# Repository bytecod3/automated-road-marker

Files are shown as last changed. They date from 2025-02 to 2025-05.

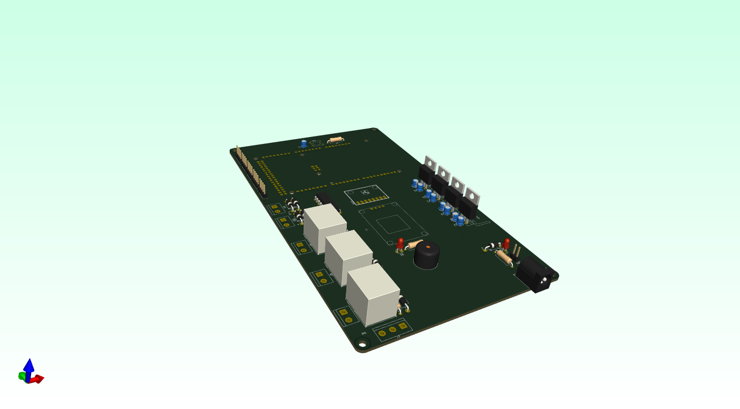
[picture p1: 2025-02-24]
hardware-design/pcb-images/side-view.png

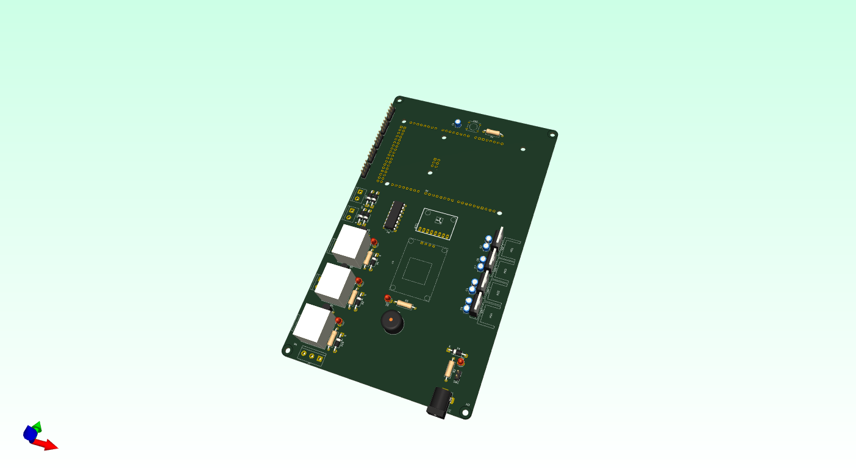
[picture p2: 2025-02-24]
hardware-design/pcb-images/v1-orthogonal.png

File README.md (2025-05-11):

# automated-road-marker
Automated road marker project

## Battery sizing and component voltages 
| Component | Voltage rating (V) | Current rating
| --- | --- | --- |
| Arduino MEGA 2560  | 7-12 | -
| TT 130 accelerator/decelerator motor  | 3-6 | 170mA(at 4.5V)
| HC-SR04 ultrasonic sensor | 5 | 4mA
|  12V Solenoid valve G1/2 DN15 BSPP Pressure Type | 12 | 416mA
| 12V DC 385 high temperature water pump | 12 | 400mA |
| YF-S401 Water Flow Sensor | 5 | 15 mA (at 5V)

Recomended Battery = 12V >2000mAh

## firmware dependencies
The following libraries need to installed in Arduino 
1. LiquidCrystal I2C library by Frank de Brabander
2. I2Cdev

## Following a straight line 
The robot follows a heading that is referenced to where it starts. To do this, 
1. place the robot on the surface you want to paint
2. press the reset button WHILE THE ROBOT IS STATIONARY! There should be no movements or shaking. 
3. The robot should follow a straight heading.
4. To stop the robot, press the ON/OFF button, or disconenct the battery 

5. If using LCD, the screen should show the flow rate.

## Paint system 
The paint sequence is as follows:
1. Once the robot is turned on, it paints at intervals of 5 seconds( this can be changed in the 
code. See code!). This paint sequence produces a dotted line 
2. Pump 1, pump 2 and solenoid are turned on at the same time.
3. Flow rate is measured and displayed. 
4. Process repeats.
5. You can increase the length of the dotted line by increasing the paint interval. (Again, see code 
comments for this)

## ultrasonic designations 

US1 -> Front ultrasonic
US2 -> Right ultrasonic
US3 -> Left ultrasonic
US4 -> Resorvoir level ultrasonic

### Ultrasonic Conclusion
Ultrasonic avidance is not necesssary in the real-world. Why are you painting a road with obstacles??

## Flow meter interrupt pin change
The schematic show flow meter signal connected to pin 10. From tests, pin 10 cannot support
interrupts. Please use pin 2 for the flow meter signal.( See code on flow meter Pin -> in defines. h. If you wish 
to change the pin to pin number 3).

Only pin 2 and 3 can be used for the flow meter.

# LCD library installation
If you cannot find the Arduino-LiquidCrystal-I2C on Arduino Library manager, copy the Arduino-LiquidCrystal-I2C folder into your Arduino installation folder.
You should be able to compile the code with no errors.

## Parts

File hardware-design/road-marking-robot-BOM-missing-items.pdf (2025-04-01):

### road-marking-robot-BOM

# | Value | Reference | Qty | DNP | SHOP

1 | Arduino_Mega2560_R3_Shield | A1 | 1
2 | MPU6050 | ACC1 | 1
3 | Buzzer | BZ1 | 1
4 | 10uf Capcaitor | C1,C2,C3,C4,C5,C6,C7,C8 | 8
5 | 100nF | C9 | 1
6 | 1N4001 | D1,D3,D4,D6,D7,D8,D9,D10 | 8
7 | 3mm Green LED | D2,D5 | 2
8 | 3mm Red LED | D11,D12,D13 | 3
9 | Heat sink | HS1,HS2,HS3,HS4 | 4 | https://www.pixelelectric.com/more-categories/other-accessories/fans-heater-coolers/heat-sink-black-anodized-to-220/
10 | DC Barrel Jack THT PCB mount | J1 | 1 | https://www.pixelelectric.com/more-categories/electronic-components/led-plugs-connectors/plugs-connectors/dc-power-jack-2-1mm-barrel-type-pcb-mount/
11 | u-sonic-1 | J2 | 1
12 | u-sonic-2 | J3 | 1
13 | u-sonic-3 | J4 | 3 | https://bluepacknova.com/product/ultrasonic-sensor/
16 | 3PIN Terminal block | J7 | 2 | https://www.pixelelectric.com/electronic-components/led-plugs-connectors/plugs-connectors/kf301-3p-5-08mm-3-pin-connector-terminal/
17 | 2PIN terminal block | J8,J11,J13 | 3
18 | 2 pin Terminal block | J9 | 3 | https://www.pixelelectric.com/more-categories/electronic-components/led-plugs-connectors/plugs-connectors/kf301-2pin-straight-pin-pcb-screw-block/
20 | SugarCube relay | K1,K2,K3 | 1 | https://bluepacknova.com/product/5v-relay-1-channel/
21 | ROBOT_WHEEL | M2 | 1 | DNP
22 | BC547 transistor | Q2,Q3,Q4 | 5 | https://store.nerokas.co.ke/SKU-845?search=bc547&description=true
23 | 500R resistor | R1,R2,R3,R5,R6 | 5
24 | 10K resistor | R4 | 1
26 | push button pin | SW2 | 1
27 | LM7909_TO220 | U1 | 1 | https://www.pixelelectric.com/more-categories/electronic-components/passive-components/transistor-mosfet/l7809cv-high-power-voltage-regulator/
28 | LM7812_TO220 | U2 | 1 | https://www.pixelelectric.com/more-categories/electronic-components/passive-components/transistor-mosfet/l7912cv-high-power-voltage-regulator/
29 | LM7805_TO220 | U3 | 1 | https://www.pixelelectric.com/more-categories/electronic-components/passive-components/transistor-mosfet/l7905cv-high-power-voltage-regulator/
30 | LM7806_TO220 | U4 | 1 | https://www.pixelelectric.com/more-categories/electronic-components/passive-components/transistor-mosfet/l7806cv-high-power-voltage-regulator/
31 | NE06M GPS Module | U5 | 1 | https://bluepacknova.com/product/gy-neo-6m-gps-active-ceramic-antenna-module/
32 | L293D Motor driver chip | U6 | 1
33 | Heat shrink tubing 5mm | | 3 meters
34 | M3 philips screws | 8 | Source locally
35 | 1cm standoffs | 8 | Source locally
36 | PCB Copper clads single side 20x15 cm | 2
37 | Hydrogen peroxide | 2 cans
38 | Dilute HCL | 1 liter
39 | Male header pins single row 2.54mm pitch | 8 strips
40 | 20AWG copper wire | 4 meters
41 | Soldering wire | 5 meters
42 | Soldering flux | 1 bottle
43 | Female header pins single row 2.54mm pitch | 4 strips | https://bluepacknova.com/product/female-header-pin-2-0-mm/

BOM-revised-missing-items-18.03.25

### Page 1

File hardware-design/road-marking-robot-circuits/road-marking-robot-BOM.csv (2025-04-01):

# | Value | Reference | Qty | DNP
1 | Arduino_Mega2560_R3_Shield | A1 | 1
2 | MU6060 | ACC1 | 1
3 | Buzzer | BZ1 | 1
4 | 10uf Capcaitor | C1,C2,C3,C4,C5,C6,C7,C8 | 8
5 | 100nF | C9 | 1
6 | 1N4001 | D1,D3,D4,D6,D7,D8,D9,D10 | 8
7 | 3mm Green LED | D2,D5 | 2
8 | 3mm Red LED | D11,D12,D13 | 3
9 | Heat sink | HS1,HS2,HS3,HS4 | 4
10 | DC Barrel Jack THT | J1 | 1
11 | u-sonic-1 | J2 | 1
12 | u-sonic-2 | J3 | 1
13 | u-sonic-3 | J4 | 1
14 | u-sonic-4 | J5 | 1
15 | u-sonic-5 | J6 | 1
16 | 3PIN Terminal block | J7 | 1
17 | 2PIN terminal block | J8,J11,J13 | 3
18 | 2 pin Terminal block | J9 | 1
19 | 2 PIN terminal Block | J10 | 1
20 | SugarCube relay | K1,K2,K3 | 3
21 | ROBOT_WHEEL | M2 | 1 | DNP
22 | BC547 transistor | Q2,Q3,Q4 | 3
23 | 500R resistor | R1,R2,R3,R5,R6 | 5
24 | 10K resistor | R4 | 1
25 | 2pin terminal block | SW1 | 1
26 | push button pin | SW2 | 1
27 | LM7909_TO220 | U1 | 1
28 | LM7812_TO220 | U2 | 1
29 | LM7805_TO220 | U3 | 1
30 | LM7806_TO220 | U4 | 1
31 | NE06M GPS Module | U5 | 1
32 | L293D Motor driver chip | U6 | 1

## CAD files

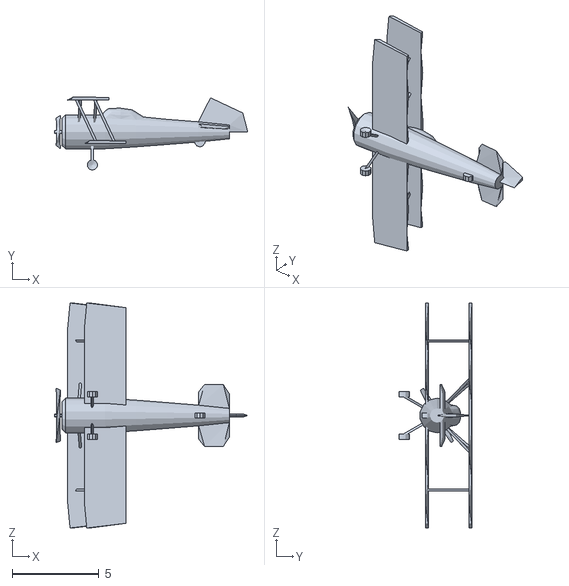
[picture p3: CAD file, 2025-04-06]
firmware/i2cdevlib-master/Arduino/MPU6050/examples/MPU6050_DMP6_using_DMP_V6.12/MPUplane/data/biplane.obj
11.2 x 4.23 x 13.0

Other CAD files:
firmware/i2cdevlib-master/PIC18/MPU6050/Examples/MPU6050_raw.X/l.obj

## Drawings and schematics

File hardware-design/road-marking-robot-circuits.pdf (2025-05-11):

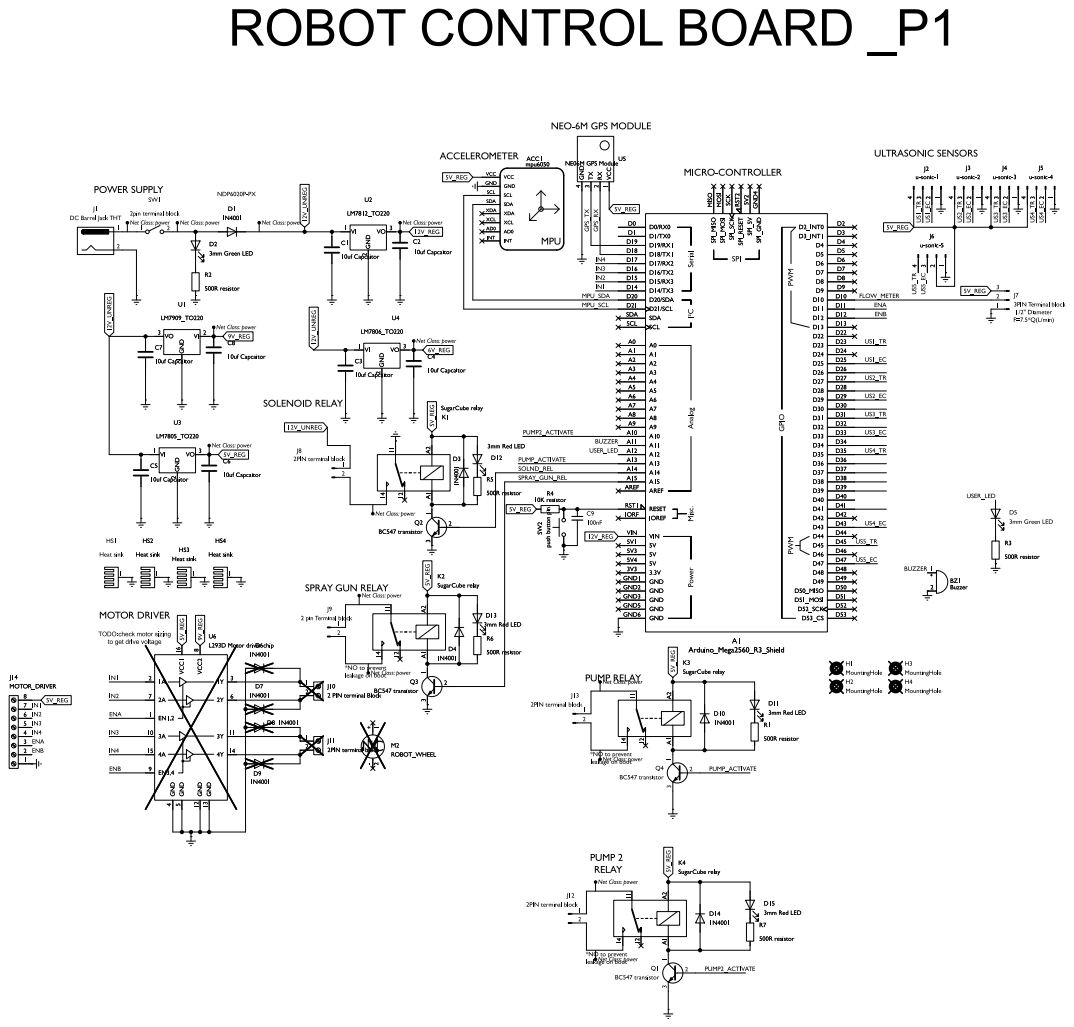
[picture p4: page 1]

leakageon boot ROBOT CONTROL BOARD _P1

leakageon boot SPRAYGUN RELAY

TODO:check motor sizing
to get drive voltage

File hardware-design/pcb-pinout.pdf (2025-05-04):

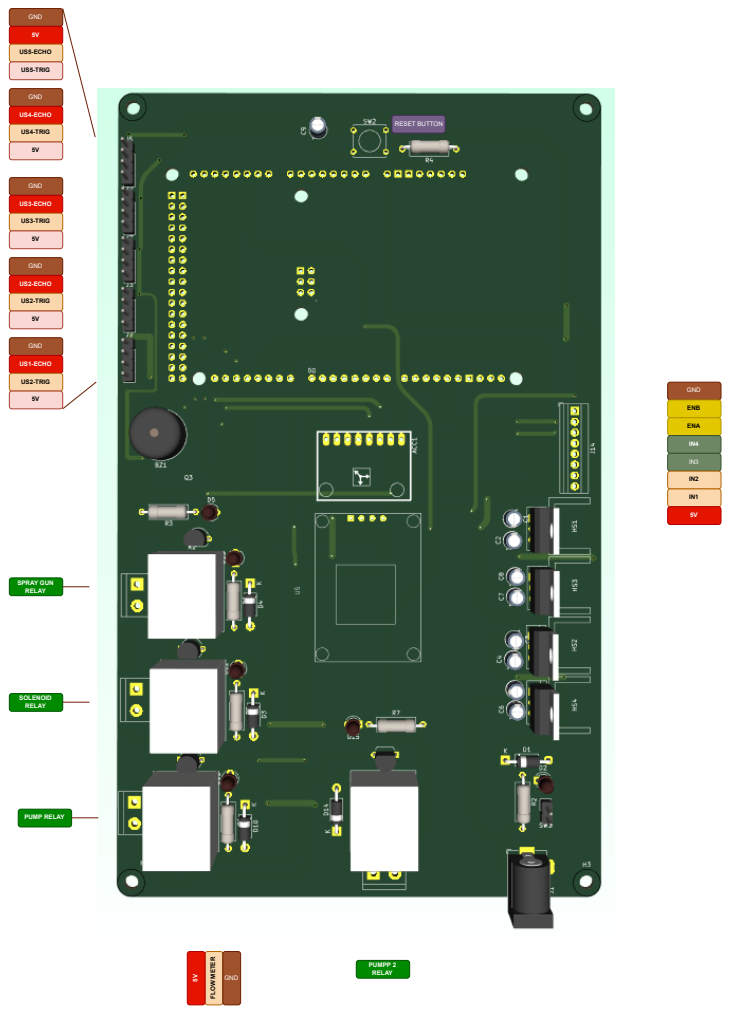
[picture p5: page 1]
GND; US5-ECHO; US5-TRIG; US4-ECHO; US4-TRIG; US3-ECHO; US3-TRIG; US2-ECHO; US2-TRIG; US1-ECHO; SPRAY GUN RELAY; PUMP RELAY; SOLENOID RELAY; PUMPP 2 RELAY; ENB; ENA; RESET BUTTON; FLOW METER

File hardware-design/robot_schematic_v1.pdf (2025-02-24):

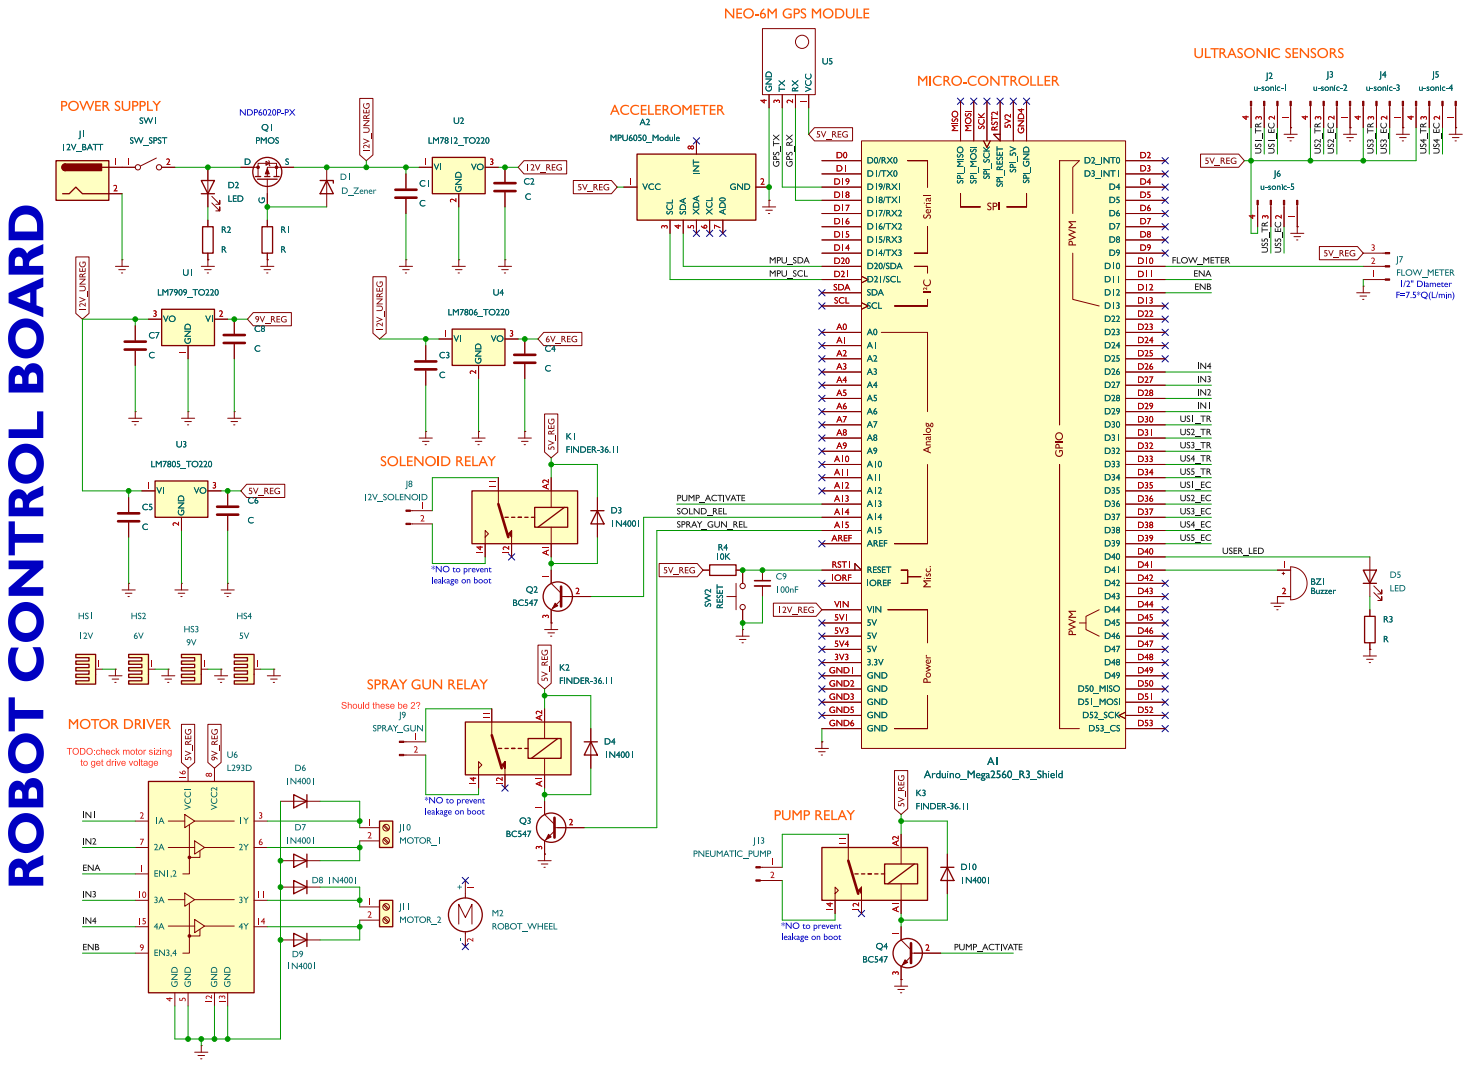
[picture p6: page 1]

Should these be 2? ROBOT CONTROL BOARD

leakageon boot TODO:check motor sizing
to get drive voltage

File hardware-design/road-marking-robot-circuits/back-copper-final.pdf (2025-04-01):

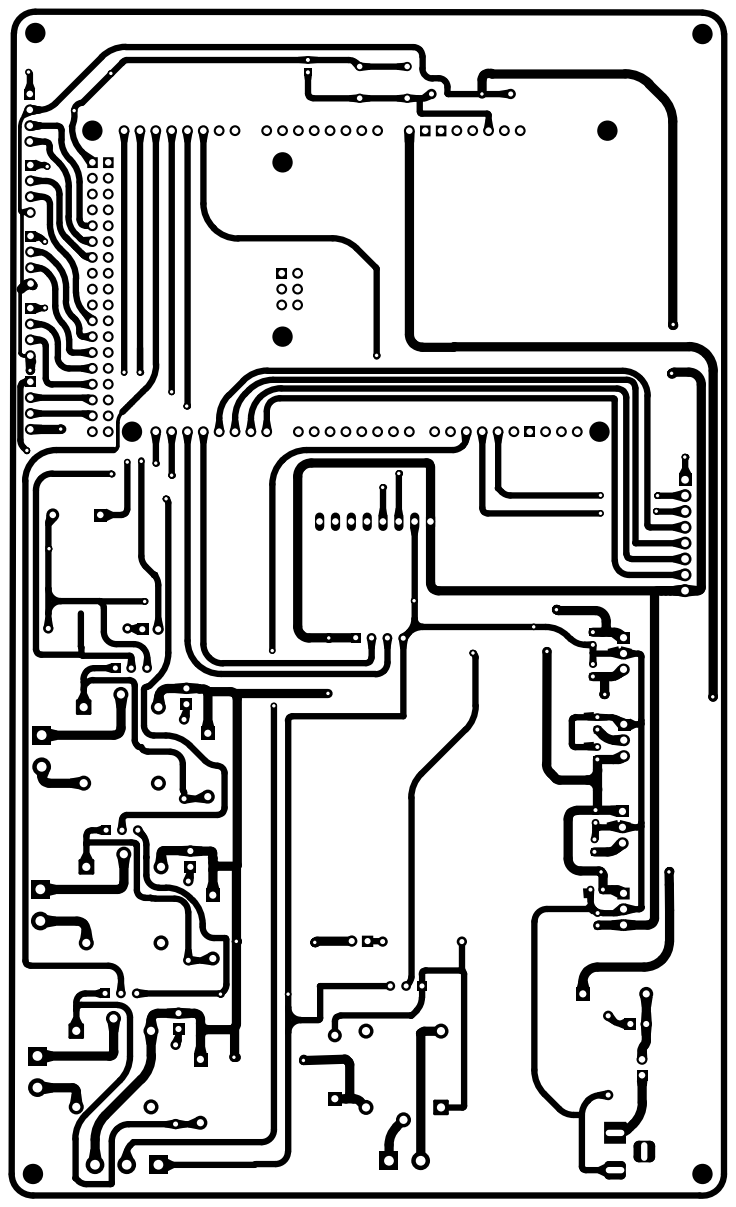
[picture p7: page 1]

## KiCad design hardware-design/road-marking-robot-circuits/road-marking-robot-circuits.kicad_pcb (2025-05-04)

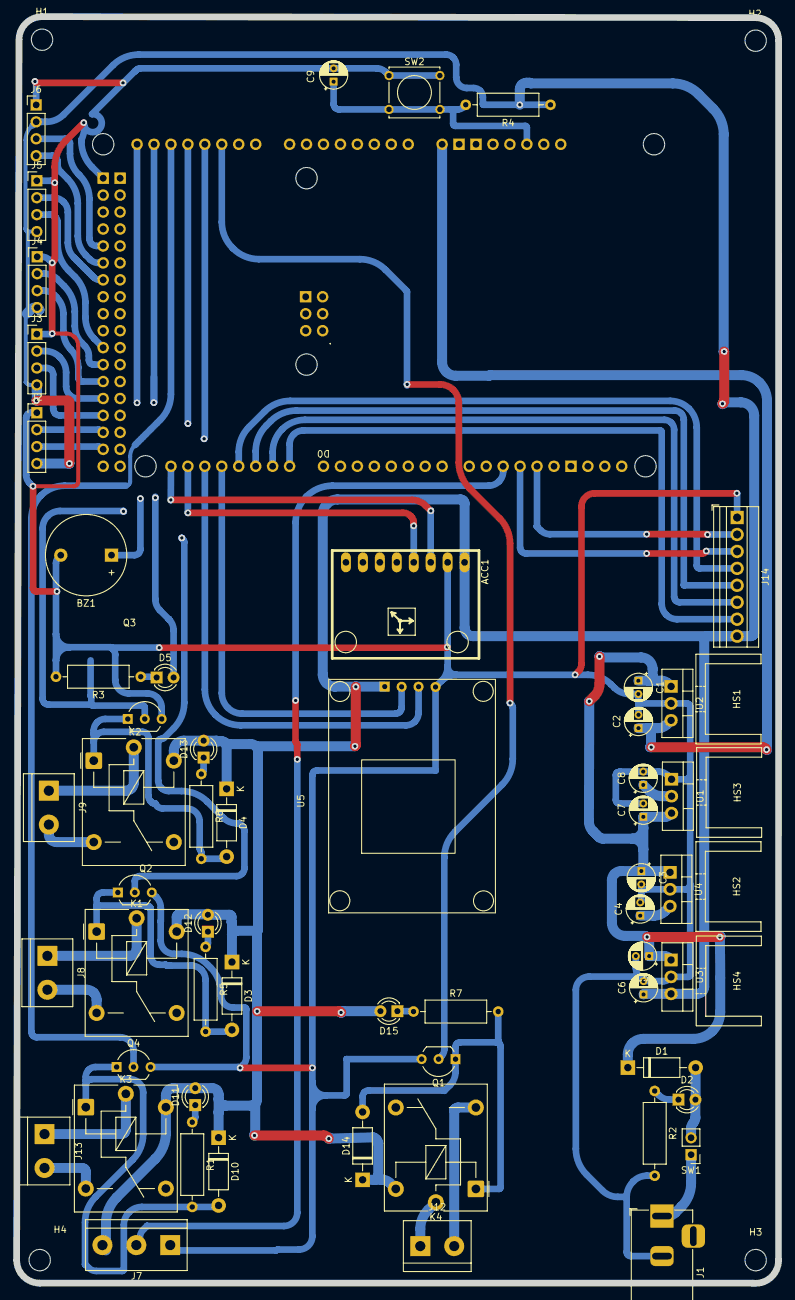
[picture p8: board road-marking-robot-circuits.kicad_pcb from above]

Board: 2 copper layers, 114.2 x 189.8 mm, 65 parts (0 on the bottom side), 53 nets.

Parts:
A1: Arduino_Mega2560_R3_Shield
ACC1: mpu6050; GY-521
BZ1: Buzzer; Buzzer_12x9.5RM7.6
C1, C2, C3, C4, C5, C6, C7, C8: 10uf Capcaitor; CP_Radial_D4.0mm_P2.00mm
C9: 100nF; CP_Radial_D4.0mm_P2.00mm
D1, D3, D4, D10, D14: 1N4001; D_DO-41_SOD81_P10.16mm_Horizontal
D2, D5: 3mm Green LED; LED_D3.0mm
D11, D12, D13, D15: 3mm Red LED; LED_D3.0mm
H1, H2, H3, H4: MountingHole; MountingHole_3.2mm_M3
HS1, HS2, HS3, HS4: Heat sink; Heatsink_Stonecold_HS-S02_13.21x9.53mm
J1: DC Barrel Jack THT; BarrelJack_Horizontal
J2: u-sonic-1; PinHeader_1x04_P2.54mm_Vertical
J3: u-sonic-2; PinHeader_1x04_P2.54mm_Vertical
J4: u-sonic-3; PinHeader_1x04_P2.54mm_Vertical
J5: u-sonic-4; PinHeader_1x04_P2.54mm_Vertical
J6: u-sonic-5; PinHeader_1x04_P2.54mm_Vertical
J7: 3PIN Terminal block; TerminalBlock_bornier-3_P5.08mm
J8, J12, J13: 2PIN terminal block; TerminalBlock_bornier-2_P5.08mm
J9: 2 pin Terminal block; TerminalBlock_bornier-2_P5.08mm
J14: MOTOR_DRIVER; TerminalBlock_Xinya_XY308-2.54-8P_1x08_P2.54mm_Horizontal
K1, K2, K3, K4: SugarCube relay; Relay_SPDT_Finder_36.11
Q1, Q2, Q3, Q4: BC547 transistor; TO-92_Inline_Wide
R1, R2, R3, R5, R6, R7: 500R resistor; R_Axial_DIN0309_L9.0mm_D3.2mm_P12.70mm_Horizontal
R4: 10K resistor; R_Axial_DIN0309_L9.0mm_D3.2mm_P12.70mm_Horizontal
SW1: 2pin terminal block; PinHeader_1x02_P2.54mm_Vertical
SW2: push button pin; SW_Tactile_Straight_KSA0Axx1LFTR
U1: LM7909_TO220; TO-220-3_Vertical
U2: LM7812_TO220; TO-220-3_Vertical
U3: LM7805_TO220; TO-220-3_Vertical
U4: LM7806_TO220; TO-220-3_Vertical
U5: NE06M GPS Module; NEO-6M-GPS-MODULE

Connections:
5V_REG: ACC1.VCC, C6.1, D3.1 (K), D4.1 (K), D10.1 (K), D11.2 (A), D12.2 (A), D13.2 (A), D14.1 (K), D15.2 (A), J2.4, J3.4, J4.4, J5.4, J6.2, J7.3, J14.8, K1.A2, K2.A2, K3.A2, K4.A2, R4.1, U3.3 (VO), U5.1 (VCC)
6V_REG: C4.1, U4.3 (VO)
9V_REG: C8.1, U1.2 (VI)
12V_REG: A1.VIN, C2.1, U2.3 (VO)
12V_UNREG: C1.1, C3.1, C5.1, C7.1, D1.1 (K), J8.1, U1.3 (VO), U2.1 (VI), U3.1 (VI), U4.1 (VI)
/BUZZER: A1.A11, BZ1.1 (+)
/ENA: A1.D11, J14.3
/ENB: A1.D12, J14.2
/FLOW_METER: A1.D10, J7.2
/GPS_RX: A1.D18 (D18/TX1), U5.2 (RX)
/GPS_TX: A1.D19 (D19/RX1), U5.3 (TX)
/IN1: A1.D14 (D14/TX3), J14.7
/IN2: A1.D15 (D15/RX3), J14.6
/IN3: A1.D16 (D16/TX2), J14.5
/IN4: A1.D17 (D17/RX2), J14.4
/MPU_SCL: A1.D21 (D21/SCL), ACC1.SCL
/MPU_SDA: A1.D20 (D20/SDA), ACC1.SDA
/PUMP2_ACTIVATE: A1.A10, Q1.2 (B)
/PUMP_ACTIVATE: A1.A13, Q4.2 (B)
/SOLND_REL: A1.A14, Q2.2 (B)
/SPRAY_GUN_REL: A1.A15, Q3.2 (B)
/US1_EC: A1.D25, J2.2
/US1_TR: A1.D23, J2.3
/US2_EC: A1.D29, J3.2
/US2_TR: A1.D27, J3.3
/US3_EC: A1.D33, J4.2
/US3_TR: A1.D31, J4.3
/US4_EC: A1.D43, J5.2
/US4_TR: A1.D35, J5.3
/US5_EC: A1.D47, J6.3
/US5_TR: A1.D45, J6.4
/USER_LED: A1.A12, D5.2 (A)
Earth: A1.GND6 (GND), ACC1.GND, BZ1.2 (-), C1.2, C2.2, C3.2, C4.2, C5.2, C6.2, C7.2, C8.2, C9.2, J1.2, J2.1, J3.1, J4.1, J5.1, J6.1, J7.1, J14.1, K1.11, Q1.3 (E), Q2.3 (E), Q3.3 (E), Q4.3 (E), R2.2, R3.2, SW2.1, U1.1 (GND), U2.2 (GND), U3.2 (GND), U4.2 (GND), U5.4 (GND)
unnamed: A1.RST1 (RESET), C9.1, R4.2, SW2.2
unnamed: D1.2 (A), D2.2 (A), SW1.2 (B)
unnamed: D2.1 (K), R2.1
unnamed: D3.2 (A), K1.A1, Q2.1 (C), R5.2
unnamed: D4.2 (A), K2.A1, Q3.1 (C), R6.2
unnamed: D5.1 (K), R3.1
unnamed: D10.2 (A), K3.A1, Q4.1 (C), R1.2
unnamed: D11.1 (K), R1.1
unnamed: D12.1 (K), R5.1
unnamed: D13.1 (K), R6.1
unnamed: D14.2 (A), K4.A1, Q1.1 (C), R7.2
unnamed: D15.1 (K), R7.1
unnamed: J8.2, K1.14
unnamed: J9.1, K2.11
unnamed: J9.2, K2.14
unnamed: J12.1, K4.11
unnamed: J12.2, K4.14
unnamed: J13.1, K3.11
unnamed: J13.2, K3.14
unnamed: J1.1, SW1.1 (A)

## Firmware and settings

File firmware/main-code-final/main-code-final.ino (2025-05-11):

#include "defines.h"
#include <Wire.h>
#include "I2Cdev.h"

#define USE_LCD 1 // if you are using an LCD, set this line to 1, otherwise set to 0

#if USE_LCD
  #include <LiquidCrystal_I2C.h>
  LiquidCrystal_I2C lcd(0x27, 16, 2);
#endif

#define MOTOR_ENABLE 1 // must be set to 1 for the motors to run
#define MPU_ENABLE 1  // must be set to 1 for the MPU to be read


unsigned long paint_interval = 5000; // change this interval to change the length of the line painted
unsigned long previous_paint_time = 0;
unsigned long current_paint_time = 0;

// this is the variable used to turn on and off the psint system -> pump1, pump2 and solenoid
// the activation of the paint system must be non-blocking 
// so that the robot stays in motion whie painting
uint8_t paint_system_state = 0; 

/**
 * 
 * states 
 IDLE - on but not painting, buzz twice,blink at 1 second
 PAINTING - actively checking straight line and running paint system, blink at 200ms
 length between IDLE and START_PAINT ~10 seconds 
 measure distance painted?
 * FLOW
 * wait for 10 seconds after setup 
 * Read the IMU 
 * Activate the paint system while checking the straightness of the line 
 * Apply PID to motor while painting 
 * 
 * For demo: paint for 30 seconds then stop 
 * deactivate paint system 
 * state == DONE_PAINTING
 * buzz 3 times at 400ms
 * blink at 1Hz
 */

 
/**
 * Sensor read functions 
 */
void read_gps_cordinates();
void get_flow_rate();

/**
 * Paint system Relay control functions 
 */
void activate_solenoid_relay(uint8_t state);
void activate_pump_one_relay(uint8_t state);
void activate_pump_two_relay(uint8_t state);
void deactivate_solenoid_relay(uint8_t state);
void deactivate_pump_one_relay(uint8_t state);
void deactivate_pump_two_relay(uint8_t state);

void initialize_hardware_pins();
void blink_non_blocking(uint16_t);
void buzz_non_blocking(uint16_t);
void onboard_blink_non_blocking();

/**
 * set pinmodes
 */
void initialize_hardware_pins() {
  pinMode(PUMP_ONE_RELAY_PIN, OUTPUT);
  pinMode(PUMP_TWO_RELAY_PIN, OUTPUT);
  pinMode(SOLENOID_VALVE_RELAY_PIN, OUTPUT);
}

/**
 * Control the paint sequence
 */
void paint_sequence(); 

/**
 * Start pump 1
 */
void activate_pump_one_relay(uint8_t state) {
  digitalWrite(PUMP_ONE_RELAY_PIN, state);
}

/**
 * Start pump 2
 */
void activate_pump_two_relay(uint8_t state) {
  digitalWrite(PUMP_TWO_RELAY_PIN, state);
}

/** 
 * Start solenoid valve
 */
void activate_solenoid_relay(uint8_t state) {
  digitalWrite(SOLENOID_VALVE_RELAY_PIN, state);
}

/**
 * Start pump 1
 */
void deactivate_pump_one_relay(uint8_t state) {
  digitalWrite(PUMP_ONE_RELAY_PIN, state);
}

/**
 * Start pump 2
 */
void deactivate_pump_two_relay(uint8_t state) {
  digitalWrite(PUMP_ONE_RELAY_PIN, state);
}

/**
 * Start solenoid valve
 */
void deactivate_solenoid_relay(uint8_t state) {
  digitalWrite(SOLENOID_VALVE_RELAY_PIN, state);
}

/**
 * Package the paint sequence
 * This function draws a dotted line after every PAINT_INTERVAL seconds
 * To change the length of the paint interval, adjust the paint_interval variable
 */
 void paint_sequence() {
  current_paint_time = millis();
  if((current_paint_time - previous_paint_time) > paint_interval) {
    previous_paint_time = current_paint_time;
    paint_system_state = !paint_system_state; // after every paint_interval, the systems will turn ON, paint, then turn OFF

    // activate the paint system 
    activate_pump_one_relay(paint_system_state);
    activate_pump_two_relay(paint_system_state);
    activate_solenoid_relay(paint_system_state);
   
  }
 }

#if MOTOR_ENABLE 
/**
 * Motor control functions 
 */
  void init_motor_pins();
  void robot_start();
  void robot_stop();
  void robot_forward(uint8_t speed);
  void robot_turn_left(uint8_t speed);
  void robot_turn_right(uint8_t speed);
  void robot_reverse();
  void robot_set_speed(uint8_t);
  void drive_straight(uint8_t speed);
  void robot_motor_test();
  void correct_speed(int my_speed);
  void compute_RTK();
#endif

#if MPU_ENABLE 
  //===================== MPU FUNCTIONS AND VARIABLES ======================
  #define MPU_ADDRESS 0x68
  #define MPU6050_RA_GYRO_ZOUT_H 0x47 //z values register adress
  #define MPU_ACCEL_RANGE 16
  #define GYRO_RANGE 250
  
  float gyro_z; // raw z register values 
  unsigned long last_time = 0;
  float dt; // differential time 
  long gyro_z0 = 221; // gyro osffset = mean value - get this value from the callibration process
  float yaw;
  float yaw_old = 0;
  float gyro_angle_z = 0; // angle variable

  void mpu_init();
  void mpu_callibrate();
  int16_t get_z_rotation();
  void calc_yaw();
  void check_straight_line();
  void read_accelerometer_values();


  // initialize mpu
  void mpu_init() {
    Wire.begin();
    Wire.beginTransmission(MPU_ADDRESS);
    Wire.write(0x6B);
    Wire.write(0); // wake up
    Wire.endTransmission(true);
    delay(1000);
  }

  // callibrate the MPU
  void mpu_callibrate() {
    // get callibratio samples
    debugln("Getting callibration samples...");
    unsigned short times = 100; // sampling times
    for(int i=0; i < times; i++) {
      gyro_z = get_z_rotation();
      gyro_z0 += gyro_z; // sum all measured values of gyro_z
    }

    debugln("Acquired samples...");
  
    gyro_z0 /= times; // compute the mean - to get the offset of the gyroscope for compensation
    debug("Z-axis Mean: "); debugln(gyro_z0);
  }

  
  // read z axis rotation
  int16_t get_z_rotation() {
    uint8_t buffer[14];
    I2Cdev::readBytes(MPU_ADDRESS, MPU6050_RA_GYRO_ZOUT_H,2, buffer);
    return ( ((uint16_t)buffer[0]) << 8) | buffer[1];
    
  }
  
  void calc_yaw() {
    unsigned long current_time = millis(); // current time (ms)
    dt = (current_time - last_time) / 1000.0; // differential time (seconds)
    last_time = current_time; // last sampling time (ms)
  
    gyro_z = get_z_rotation();
  
    float angular_z = (gyro_z - gyro_z0) / 131.0 * dt;
    if(fabs(angular_z) < 0.05) {
      angular_z = 0.00;
    }
  
    gyro_angle_z += angular_z; // return the z axis absolute rotation integral
    yaw = -gyro_angle_z;

    // debug
    //debug("GyroZ Value: "); debug(gyro_z); debug("       GyroAngle: "); debugln(gyro_angle_z);    
  }
  
  //======================= END OF MPU FUCNTIONS AND VARIABLES ==============

#endif

// motor control variables
unsigned long t1 = 0;
unsigned long t2 = 0;

// timing variables
long int now = 0;
long int last_millis = 0;
long int current_millis = 0;
uint16_t interval = 300;

boolean buzz_state = LOW;
boolean user_led_state = LOW;

#if MOTOR_ENABLE // must be set to 1 to run motors
 
  // Adjust these speeds based on the weight of the robot
  // high speed is the max speed the robot will run at 
  // low speed is the minimum speed the robot will run at 
  // my_speed is the normal operation speed the robot should run at
  uint8_t high_speed = 54;  
  uint8_t low_speed = 20;
  uint8_t my_speed = 45;
  
  uint8_t correct_speed_right;
  uint8_t correct_speed_left;
  
  // motor driver functions 
  void init_motor_pins() {
    pinMode(ENA, OUTPUT);
    pinMode(ENB, OUTPUT);
    pinMode(IN1, OUTPUT);
    pinMode(IN2, OUTPUT);
    pinMode(IN3, OUTPUT);
    pinMode(IN4, OUTPUT);
  
    // turn off motor - initial state
    //digitalWrite(IN1, LOW);
    //digitalWrite(IN2, LOW);
    //digitalWrite(IN3, LOW);
    //digitalWrite(IN4, LOW);
  }
  
  /**
   * set motor speed
   */
  void robot_set_speed(uint8_t speed) {
    analogWrite(ENA, speed); 
    analogWrite(ENB, speed);
  }

  /**
   * Turn Left
   */
   void robot_left(uint8_t speed) {
    analogWrite(ENA, speed);
    digitalWrite(IN1, LOW); // right motor drive forward
    digitalWrite(IN2, HIGH);

    analogWrite(ENB, speed); 
    digitalWrite(IN3, HIGH); // reverse left motor, the robot will turn left
    digitalWrite(IN4, LOW); 
   }

   /**
    * Turn Right
    */
  void robot_right(uint8_t speed) {
    analogWrite(ENB, speed);
    digitalWrite(IN3, LOW); // left motor drive forward
    digitalWrite(IN4, HIGH);

    analogWrite(ENA, speed); 
    digitalWrite(IN1, HIGH); // reverse right motor, the robot will turn right
    digitalWrite(IN2, LOW); 
  }
  
  /**
   * stop robot
   */
  void robot_stop(){
    digitalWrite(IN1, LOW);
    digitalWrite(IN2, LOW);
    digitalWrite(IN3, LOW);
    digitalWrite(IN4, LOW);
  }
  
  /**
   * move robot forward
   */
  void robot_forward(uint8_t speed) {

    drive_straight(speed);

    analogWrite(ENA, correct_speed_right); // right motor
    analogWrite(ENB, correct_speed_left); // left motor
    
    digitalWrite(IN1, LOW);
    digitalWrite(IN2, HIGH);
    digitalWrite(IN3, LOW);
    digitalWrite(IN4, HIGH);
  }
  
  /**
   * reverse robot
   */
  void robot_reverse() {
    digitalWrite(IN1, HIGH);
    digitalWrite(IN2, LOW);
    digitalWrite(IN3, HIGH);
    digitalWrite(IN4, LOW);
  }
  
  /**
   * test the robot motors
   */
  void robot_motor_test() {
    robot_forward(100);
    delay(3000);
    robot_reverse();
    delay(3000);
    robot_stop();
  }

  void correct_speed(int my_speed){
    calc_yaw();
    int kp = 5; // Proportional constant 
    int error = yaw;
    correct_speed_right = my_speed + (error * kp); // maintain speed by speeding up right motor
    correct_speed_left = my_speed - (error * kp);
    
    if(correct_speed_right > high_speed) {
      correct_speed_right = high_speed; // high_speed is the maximum speed of the robot
    } else if(correct_speed_right < low_speed) {
      correct_speed_right = low_speed; // low_speed is the minimum speed of the car
    }

    // if direction changes, 
    if(correct_speed_left > high_speed){
      correct_speed_left = high_speed;
    } else if(correct_speed_left < low_speed) {
      correct_speed_left = low_speed;
    }
    
  }

  void drive_straight(uint8_t speed) {
    static unsigned long onTime;
    // to compute corr_speed, the yaw data is acquired at startup, and updated every 10 ms
    if(millis() - onTime > 10) {
      correct_speed(speed);
      onTime = millis();
    } 
  }

#endif

 /**
  * Other functions
  */

/**
 * non blocking buzz
 */
void buzz_non_blocking(uint16_t j) {
  current_millis = millis();
  if(current_millis - last_millis >= j) {
    last_millis = current_millis;
    buzz_state = !buzz_state;
    digitalWrite(BUZZER, buzz_state);
  }
}

/**
 * non blocking blink
 */
void blink_non_blocking(uint16_t i) {
  current_millis = millis();
  if(current_millis - last_millis >= i) {
    last_millis = current_millis;
    user_led_state = !user_led_state;
    digitalWrite(USER_LED, user_led_state);
  }
  
}

/**
 * ======================== FLOW METER =======================
 */

double flow_rate = 0.0; // this is the value we intend to calculate
volatile int pulse_count = 0; 

void initialize_flow_meter();
void flow();
void measure_flow_rate();

unsigned long previous_flow_time = 0;
unsigned long current_flow_time = 0;
unsigned long flow_interval = 1000; // interval to measure flow rate
uint8_t is_waiting_flow = false;

void initialize_flow_meter() {
  pinMode(FLOW_PIN, INPUT);
  digitalWrite(FLOW_PIN, HIGH);
  attachInterrupt(digitalPinToInterrupt(FLOW_PIN), flow, RISING); 
}

void flow() {
  pulse_count++;
}

void measure_flow_rate() {
  current_flow_time = millis();
  if(current_flow_time - previous_flow_time >= flow_interval) {
    previous_flow_time = current_flow_time;
    if(pulse_count != 0){

      // start flow rate conversion
  
      // check the flow sensor you are using 
      // I used FS300A with a flow range of 1-60L/min -> 
      // converting this gives 60000ml/(60*60)seconds = 16.67 ml per second
      flow_rate = (pulse_count * 16.67);
      flow_rate = flow_rate * 60; // ml per second 
      flow_rate =  flow_rate / 1000; // ml to liters- > giving you Ltrs/min
    
      #if USE_LCD
        // display on LCD
        lcd.clear();
        lcd.setCursor(1, 0);
        lcd.print("Flow rate");
        lcd.setCursor(1,1);
        lcd.print(flow_rate);
        lcd.setCursor(8, 1);
        lcd.print("L/min");
      #endif

      // reset pulse counter
      pulse_count = 0;  
    } else {
      flow_rate = 0.0;
      #if USE_LCD
        // display on LCD
        lcd.clear();
        lcd.setCursor(1, 0);
        lcd.print("Flow rate");
        lcd.setCursor(1,1);
        lcd.print(flow_rate);
        lcd.setCursor(8, 1);
        lcd.print("L/min");
      #endif
    }

    debug("FLOW_RATE: "); debugln(flow_rate); 
  }

  
}

 /**
  * ==========================================================
  */

#if USE_LCD
  /**
   * 
   * LCD screen 
   */

   
   void init_lcd();
   
   void init_lcd() {
    lcd.begin();
    lcd.clear();
    lcd.backlight(); 

    // hello message
    lcd.setCursor(1, 0);
    lcd.print("Hello, Robot");
    lcd.setCursor(1,1);
    lcd.print("Ready");
   }
#endif

void setup() {
  Serial.begin(9600);
  pinMode(BUZZER, OUTPUT);
  pinMode(USER_LED, OUTPUT);
  initialize_hardware_pins(); // setup relay pins
  initialize_flow_meter(); // set up flow meter

  #if MPU_ENABLE
    mpu_init();
    mpu_callibrate();
  #endif

  #if MOTOR_ENABLE
    // initialize motor hardware
    init_motor_pins();
    //robot_set_speed(70);
    //robot_motor_test();
  #endif

  yaw = 0;

  #if USE_LCD
    init_lcd();
  #endif
  
}


void loop() {

  /**
   * start moving the robot
   */
  robot_forward(my_speed); // go forward
  
  //debug("YAW: "); debug(yaw); debug(" Right-speed: "); debug(correct_speed_right); debug(" Left-speed: "); debugln(correct_speed_left);

  /**
   * Activate the paint system
   */
   paint_sequence();

   /**
    * Measure the flow rate
    */
   measure_flow_rate();
  
}

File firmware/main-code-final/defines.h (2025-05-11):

#ifndef DEFINES_H
#define DEFINES_H

#define debug(x) Serial.print(x)
#define debugln(x) Serial.println(x)


#define BUZZER A11
#define USER_LED A12


// MOTOR DRIVER PINS
#define ENA 11
#define ENB 12
#define IN1 14
#define IN2 15
#define IN3 16
#define IN4 17

// paint system pins
#define PUMP_ONE_RELAY_PIN        A13
#define PUMP_TWO_RELAY_PIN        A10
#define SOLENOID_VALVE_RELAY_PIN  A14
#define FLOW_PIN 2 // flow meter pin


#endif

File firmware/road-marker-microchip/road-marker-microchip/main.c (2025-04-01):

/*
 * road-marker-microchip.c
 *
 * Created: 2/24/2025 3:13:05 PM
 * Author : PC
 */ 

#define F_CPU 16E6
#include <avr/io.h>

// initialization functions - ULTRASONIC, MPU, GPS, FLOW METER, MOTORS, UART, ADC, PWM, TIMERS, RESET SYSTEM, 
// Solenoid ports

// read function - ULTRASONIC, MPU, GPS, FLOW METER

// output actuation
// check functions 
// emergency buttons

int main(void)
{
    while (1) 
    {
    }
}

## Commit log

2024-11-21 initilizes project structure
    [road-marking-robot-circuits.kicad_pcb, road-marking-robot-circuits.kicad_sch]
2024-11-30 adds motor driver
2024-11-30 adds battery estimation
2025-02-13 [ADDS] power supply
    [core.kicad_pcb, core.sch, road-marking-robot-circuits.kicad_sch]
2025-02-13 [ADDS] solenoid valve relay
    [road-marking-robot-circuits.kicad_sch]
2025-02-24 adds footprints
    [road-marking-robot-circuits.kicad_pcb, road-marking-robot-circuits.kicad_sch]
2025-02-24 [UPDATES] arduino position
    [road-marking-robot-circuits.kicad_pcb, road-marking-robot-circuits.kicad_sch]
2025-02-24 [UPDATES] PCB design
    [road-marking-robot-circuits.kicad_pcb, road-marking-robot-circuits.kicad_sch]
2025-04-01 updates FIRMWARE for ARDUINO
    [road-marking-robot-BOM-missing-items.xls, road-marking-robot-BOM.csv, road-marking-robot-circuits.kicad_pcb]
2025-04-06 [ADDS] yaw calculation
    [biplane.obj, l.obj, road-marking-robot-circuits.kicad_sch]
2025-05-04 adds motor control code
    [road-marking-robot-circuits.kicad_pcb]
2025-05-10 ADDS z axis offset error
    [main-code-final.ino]
2025-05-10 ADDS Yaw angle measurement
2025-05-11 ADDS left right motor
2025-05-11 FIXES the paint system
    [defines.h, main-code-final.ino]
2025-05-11 ADDS working code WITHOUT ULTRASONIC
